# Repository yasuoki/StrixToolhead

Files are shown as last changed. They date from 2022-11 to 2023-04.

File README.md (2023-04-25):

# Strix Tool Head for VORON TRIDENT
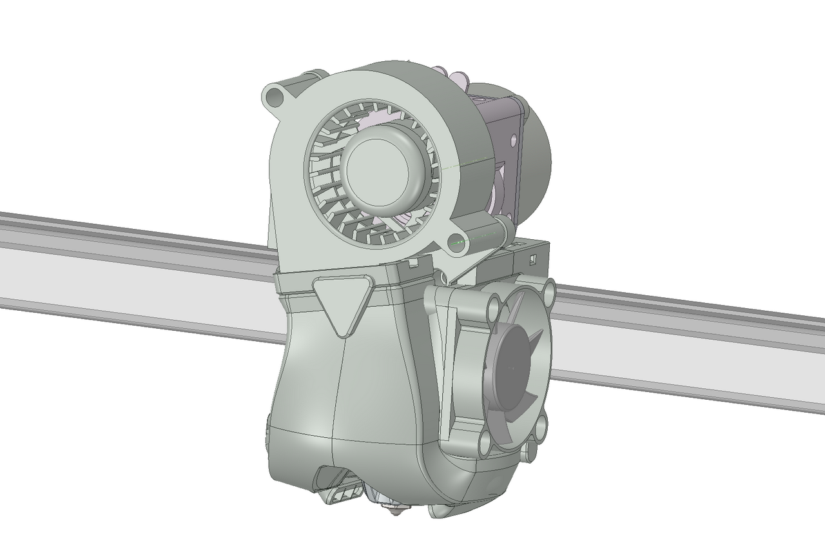
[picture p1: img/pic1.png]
<br>
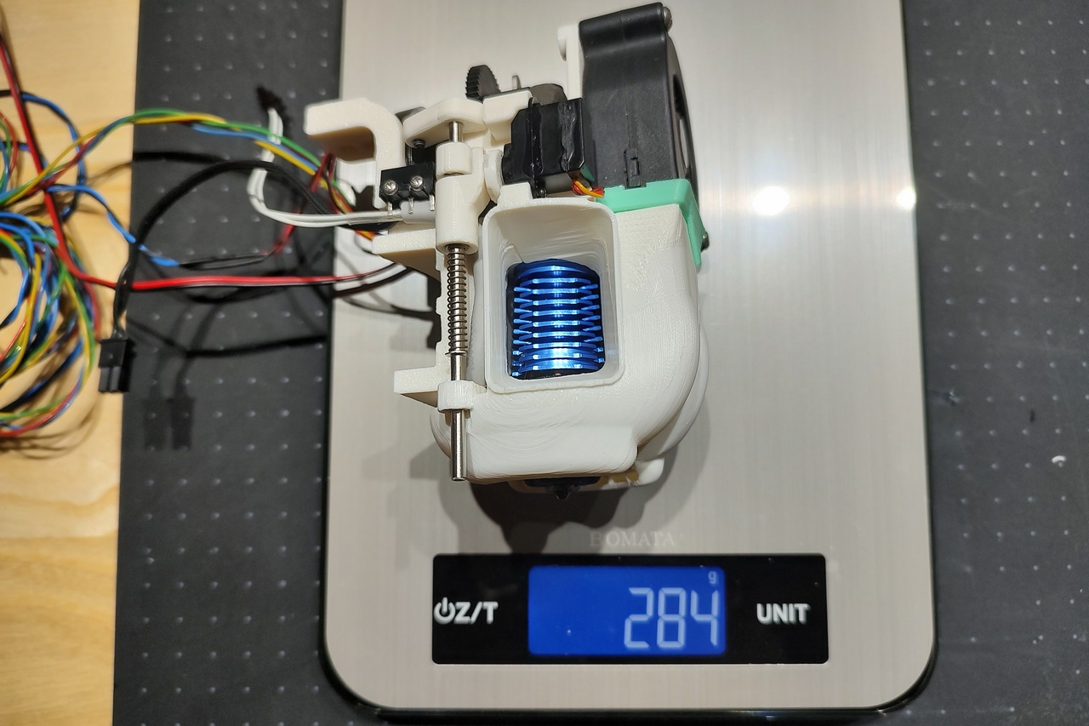
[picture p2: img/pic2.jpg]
<br>
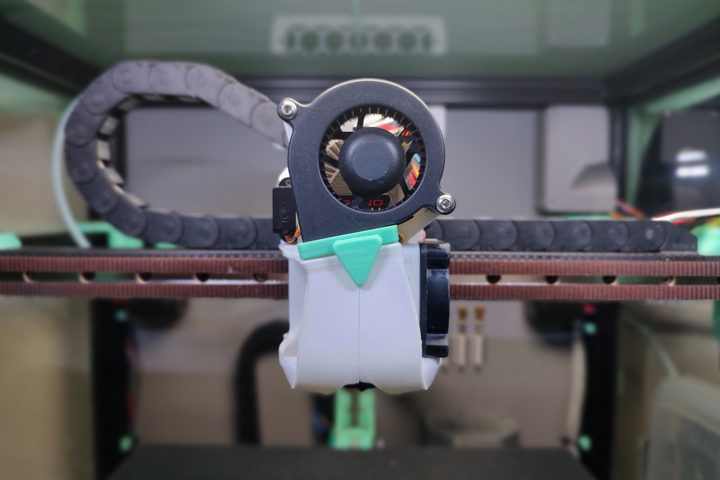
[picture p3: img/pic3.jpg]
<br>
(https://www.youtube.com/watch?v=hcAJJV4R7ww)<br>
(https://www.youtube.com/watch?v=_O_6WqJrIEA)

## Caution
This toolhead is still under development and has not yet been tested for stability.   
I am trying to design a better toolhead, but something could go wrong and your 3D printer could break.

## Features
- Short distance from the linear rail to the nozzle.
- Light weight. (290g or less)
- Optimized airflow.
- 5020 parts cooling fan.
- Built-in retractable Z-probe.
- Silent

## Probe Accuracy
~~~
PROBE_ACCURACY
PROBE_ACCURACY at X:150.000 Y:150.000 Z:5.133 (samples=10 retract=3.000 speed=10.0 lift_speed=10.0)
probe at 150.000,150.000 is z=2.132250
probe at 150.000,150.000 is z=2.133500
probe at 150.000,150.000 is z=2.134437
probe at 150.000,150.000 is z=2.134437
probe at 150.000,150.000 is z=2.134750
probe at 150.000,150.000 is z=2.134750
probe at 150.000,150.000 is z=2.133812
probe at 150.000,150.000 is z=2.134437
probe at 150.000,150.000 is z=2.133812
probe at 150.000,150.000 is z=2.134750
probe accuracy results: maximum 2.134750, minimum 2.132250, range 0.002500, average 2.134094, median 2.134437, standard deviation 0.000745
~~~

## Parts Printing
- Layer height 0.2mm, Extrusion width 0.4mm, Wall count 4, Top/Bottom layers 8, Infill 40%.
- Lightness and strength are prioritized over ease of printing, so most parts require support.
- Select ServoHorn2.2gA(B).stl and ServoHorn2gA(B).stl according to your servo motor
- Servo horns A and B differ in thickness by 0.2 mm. Select the one that fits.

## BOM
- M2.5 x 6mm BHCS x4 (for Rapido hotend)
- M3 x 8mm BHCS x4 (for linear rail)
- M3 x 10mm BHCS x7
- M3 x 25mm BHCS x2
- M3 x 35mm SHCS x2
- M2 x 10mm Self-Tapping Screw x2
- M1.7 x 3mm Flat Head Screw x1 (for servo horn)
- M1.7 x 5mm x2 (for servo mount)
- M3 x 6mm Set Screw x1
- M3 x 4mm Insert Nut x12
- 3mm(ID) x 5mm(OD) x 5mm(L) Sleeve Bearing(Oilless Bushings) x4
- 3mm(D) x 82mm(L) Stainless Steel Shaft x1
- 0.8mm(D) x 6mm(L) Piano wire x1 
- 2mm(ID) E-Clip x2
- 4mm(OD) x 0.4mm(RD) x 25mm(L) Compression Spring x1
- 26mm(L) PTFE Tube x1
- 7mm x 20mm x 0.5mm Carbon fiber plate x1 (Option)
- Micro Switch (OMRON D2F-01F Low operating force 0.74 N) x1
- Servo Motor 2.2g(Rrlandoo AS0022) or 2g(Dspower DS-M005) x1
- 5020 Blower Fan (Sunon GB1205PKV3-8AY or GDSTIME GDB5030) x1
- 4010 Axial Fan x1
- Phaetus Rapido HF x1
- Bondtech LGX Lite x1

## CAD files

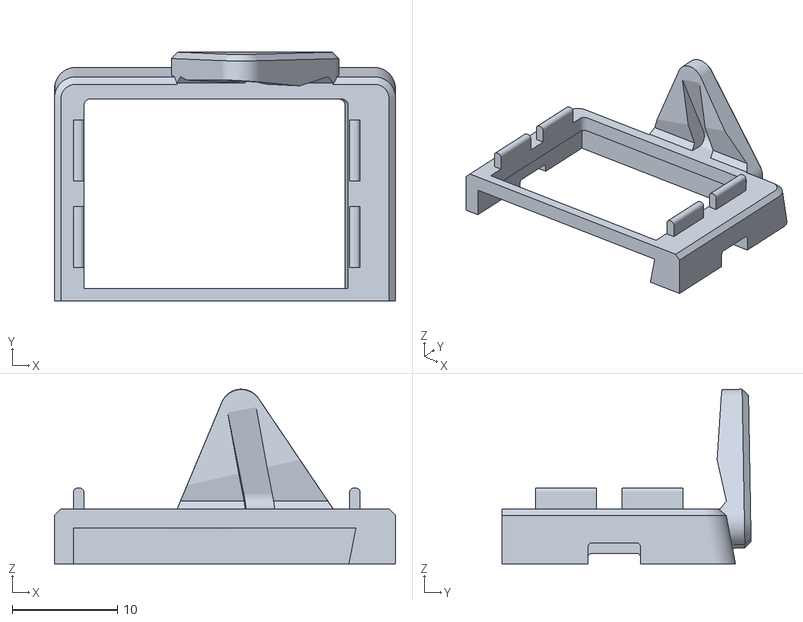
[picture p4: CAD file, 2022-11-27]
STLs/BlowerFlange.stl
32.4 x 23.7 x 16.6

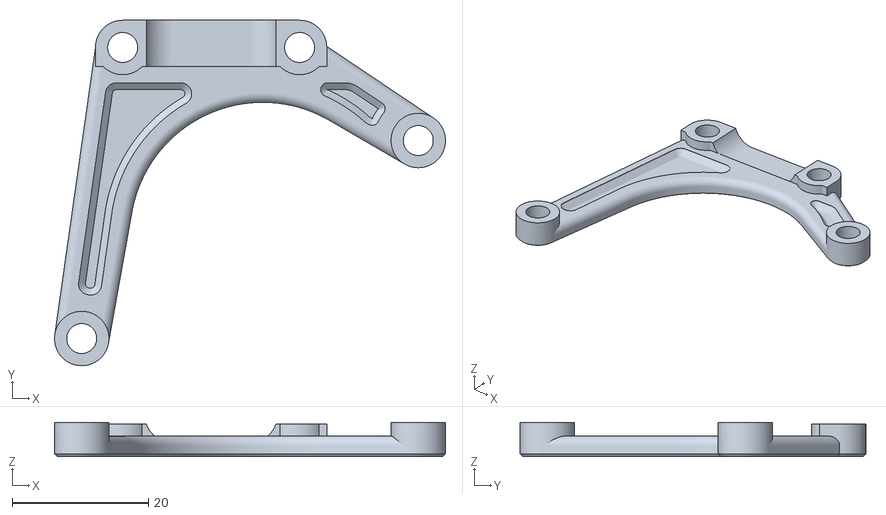
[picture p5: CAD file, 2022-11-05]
STLs/BlowerMount.stl
57.5 x 50.8 x 5.00

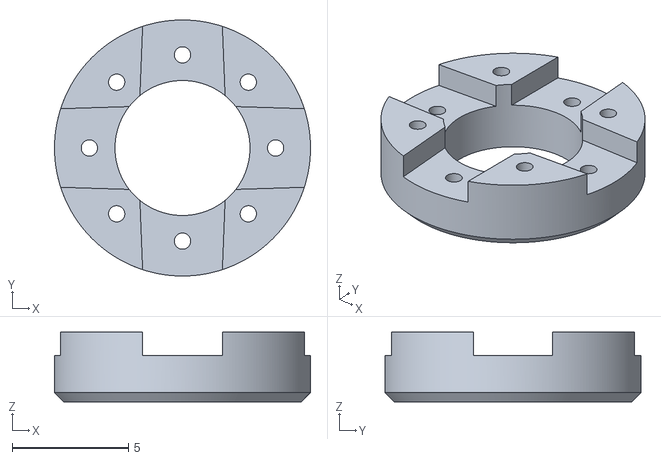
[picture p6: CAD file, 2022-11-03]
STLs/ServoHorn2gA.stl
11.0 x 11.0 x 3.00

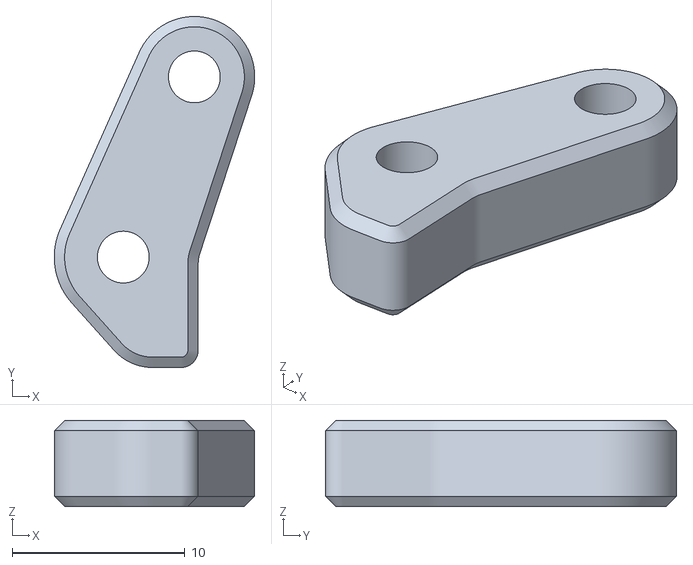
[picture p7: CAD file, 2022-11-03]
STLs/SensorTrigger.stl
11.6 x 20.3 x 5.00

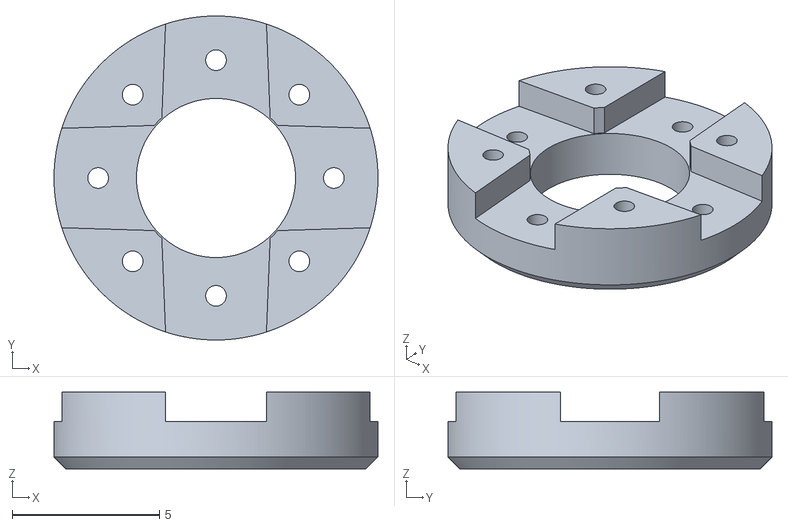
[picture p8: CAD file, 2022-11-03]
STLs/ServoHorn2.2gB.stl
11.0 x 11.0 x 2.60

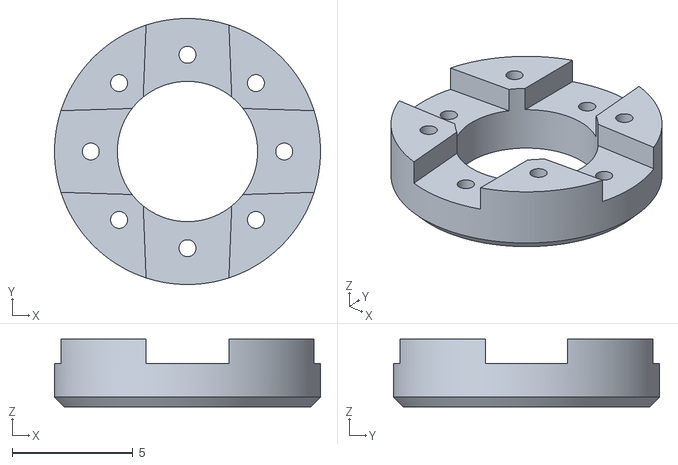
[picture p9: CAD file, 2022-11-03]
STLs/ServoHorn2gB.stl
11.0 x 11.0 x 2.80

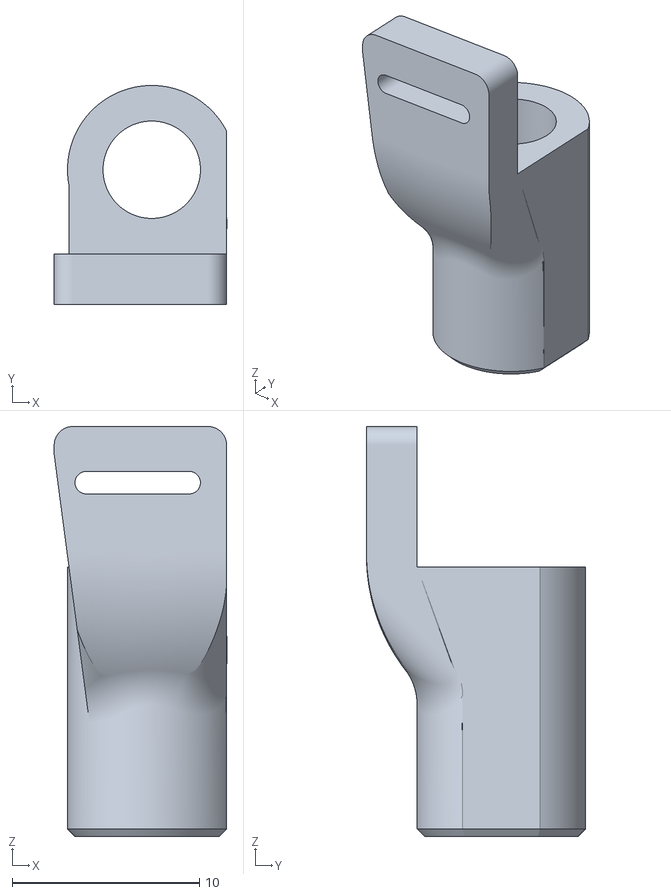
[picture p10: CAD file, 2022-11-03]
STLs/SensorElevator.stl
9.22 x 11.7 x 21.9

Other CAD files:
STLs/ServoHorn2.2gA.stl

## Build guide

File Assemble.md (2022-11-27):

## Insert nuts
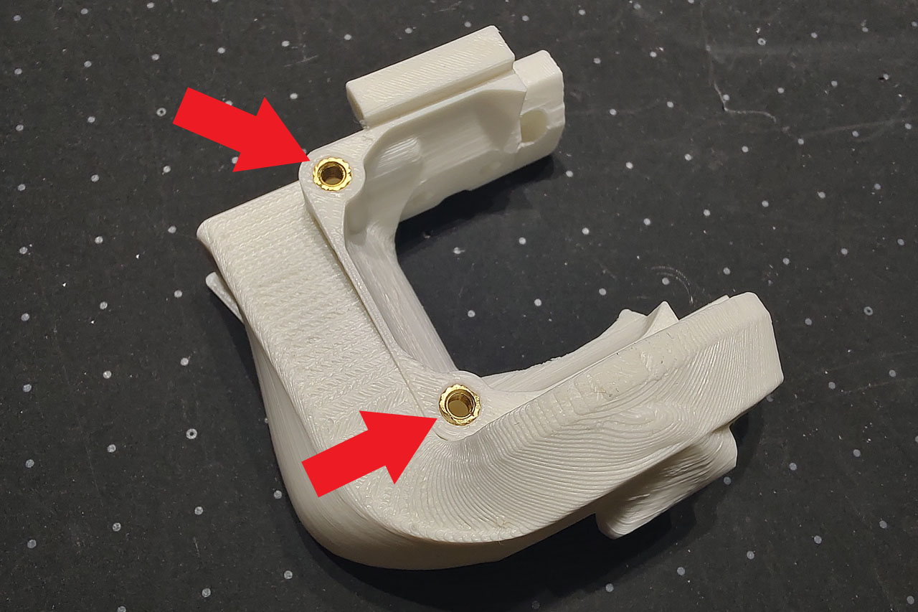
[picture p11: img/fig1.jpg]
<br>
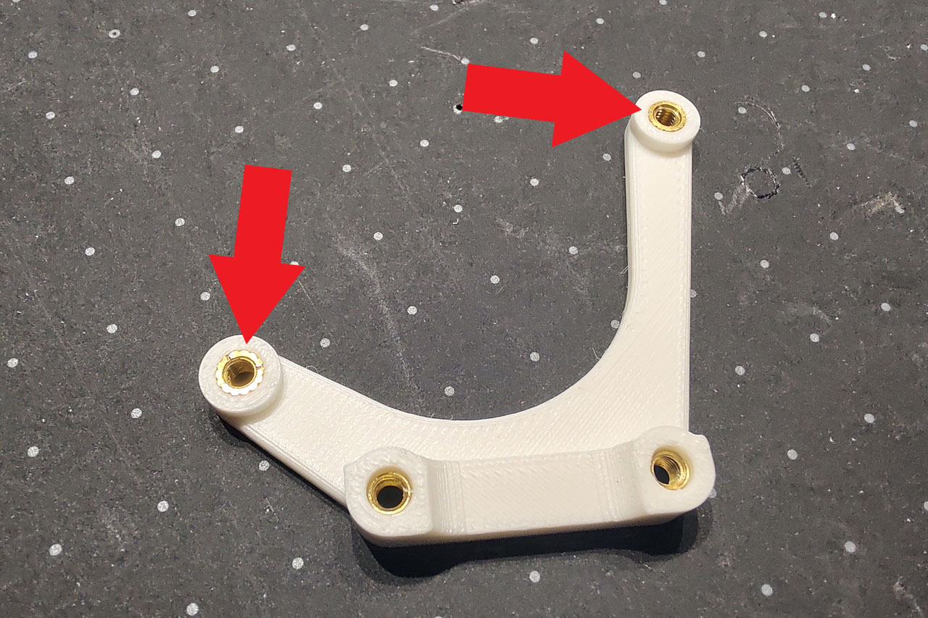
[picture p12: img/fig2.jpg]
<br>
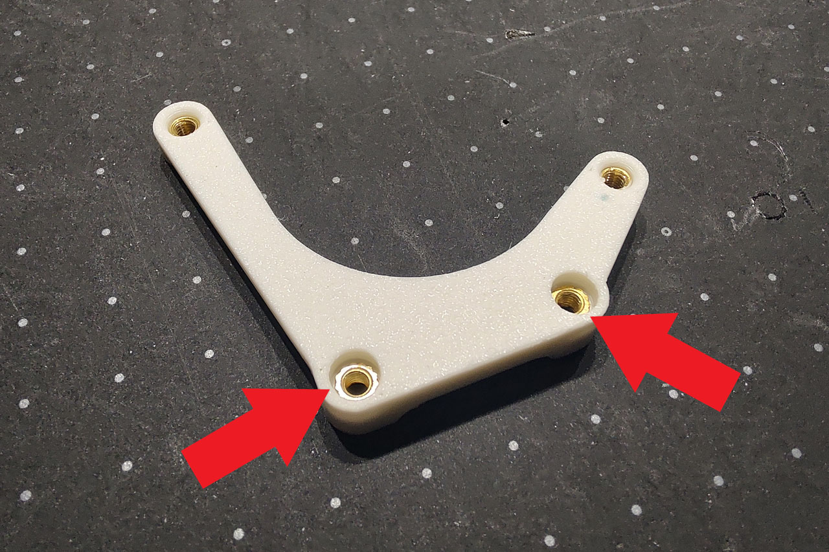
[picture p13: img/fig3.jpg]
<br>
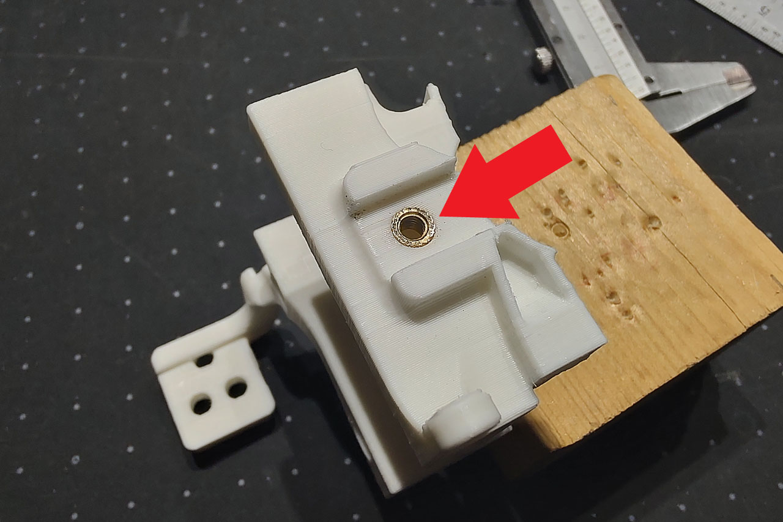
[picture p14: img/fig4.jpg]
<br>
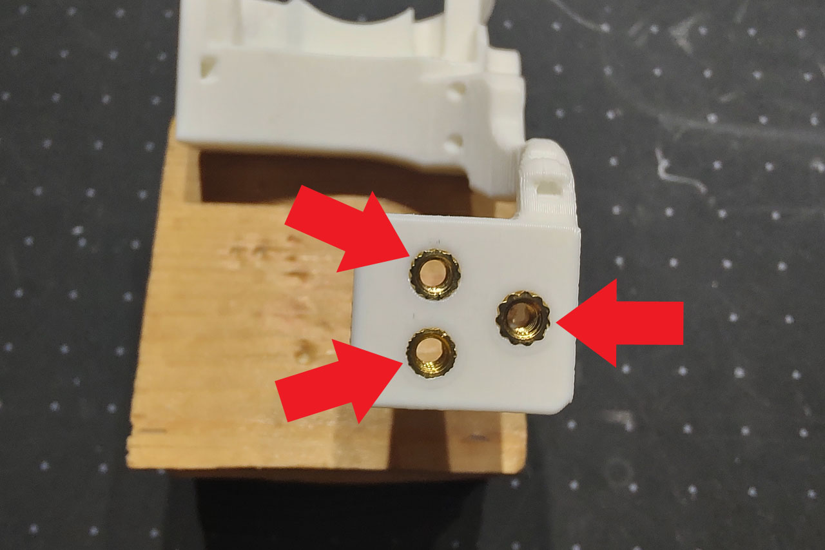
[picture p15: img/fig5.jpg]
<br>
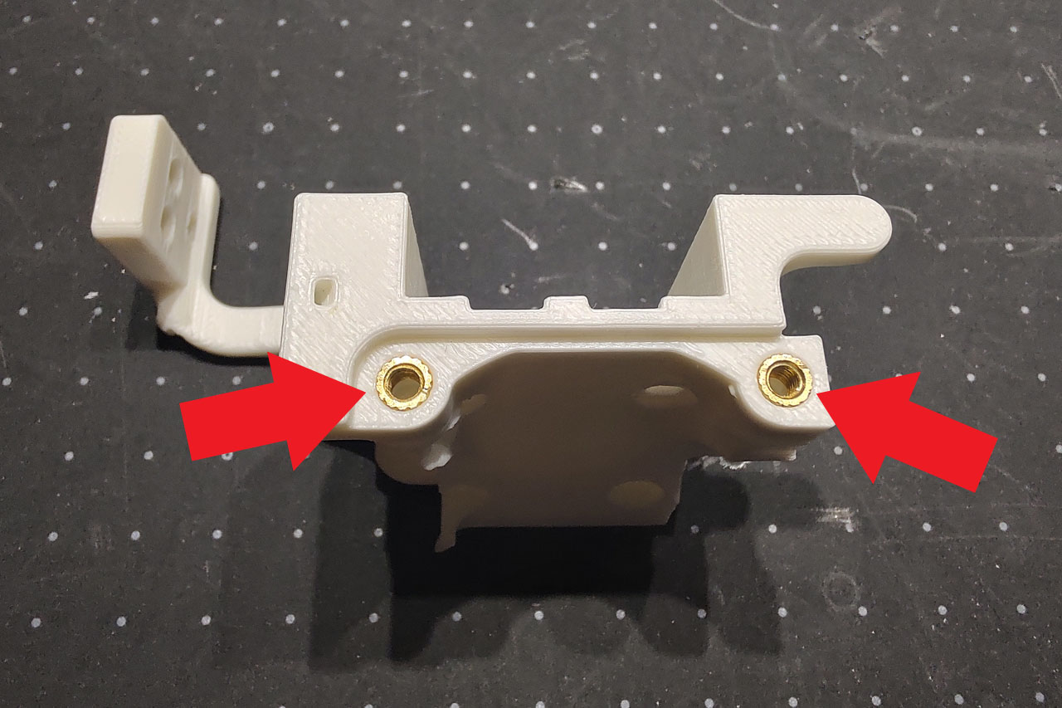
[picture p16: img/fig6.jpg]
<br>

## Sleeve bearings
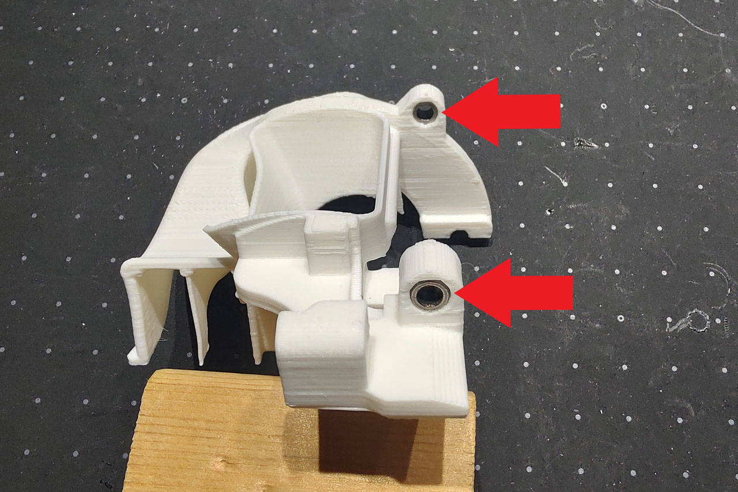
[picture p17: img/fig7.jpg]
<br>
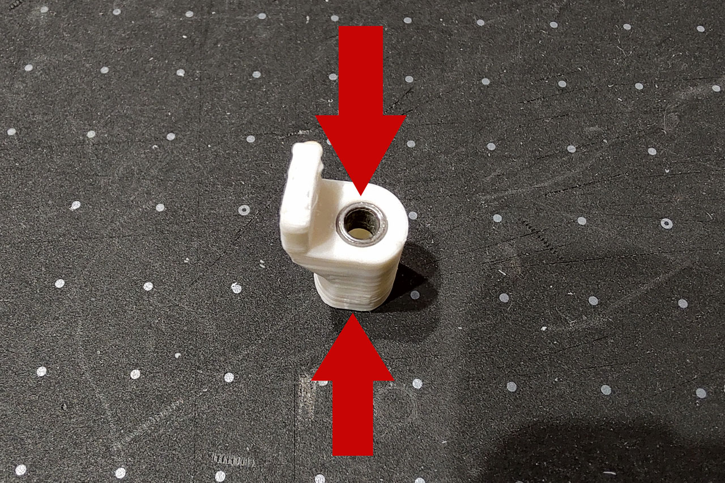
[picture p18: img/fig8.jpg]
<br>

## Z Probe
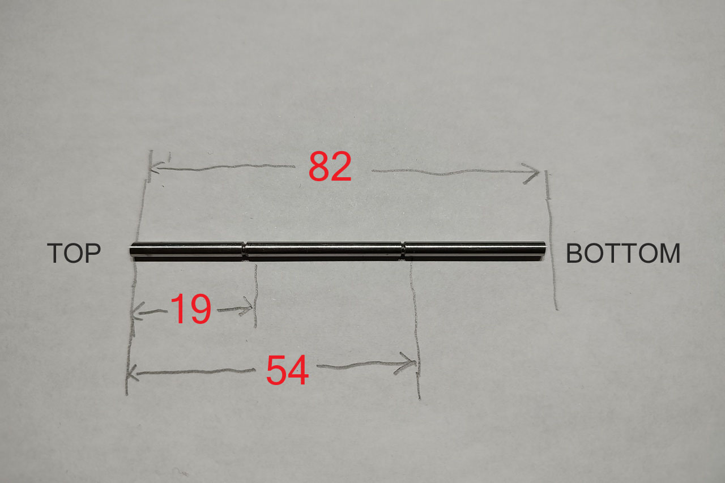
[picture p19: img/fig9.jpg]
<br>
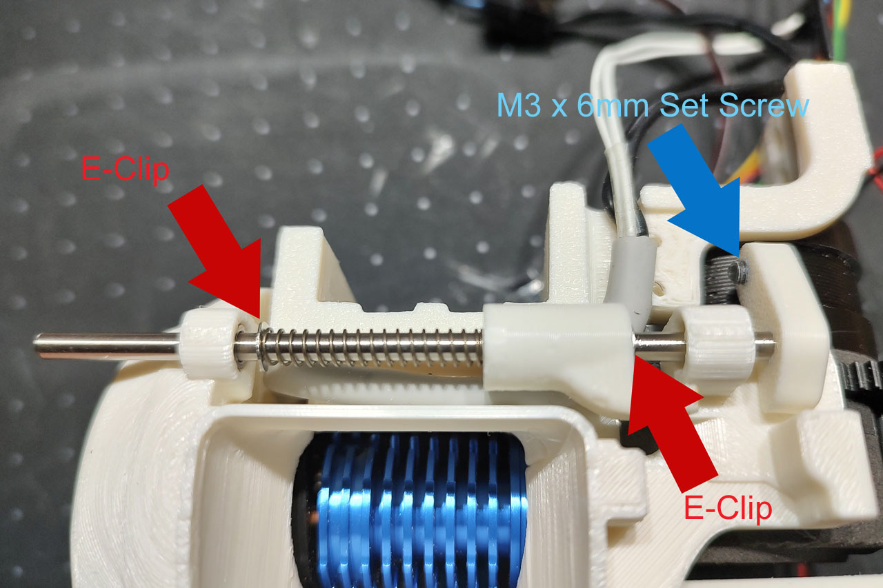
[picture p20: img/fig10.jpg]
<br>
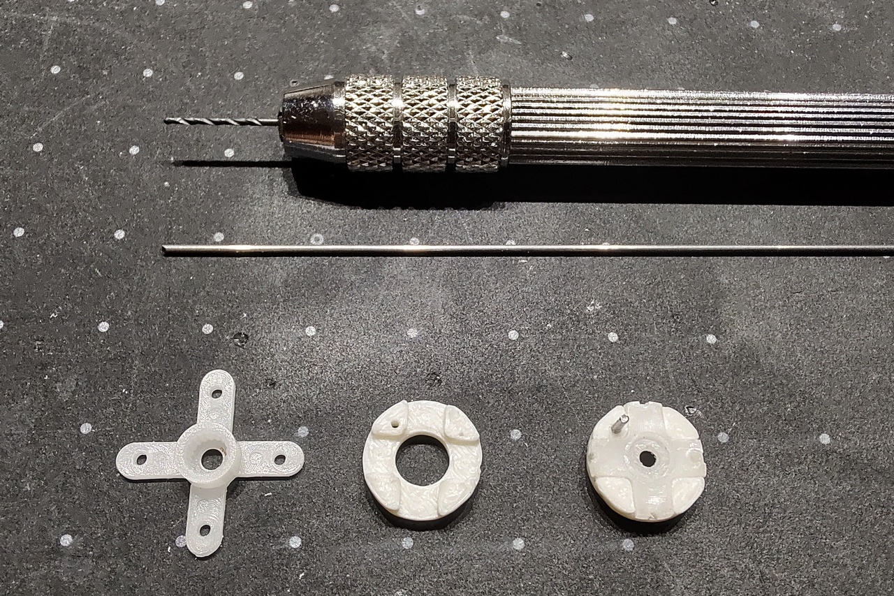
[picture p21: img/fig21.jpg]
<br>
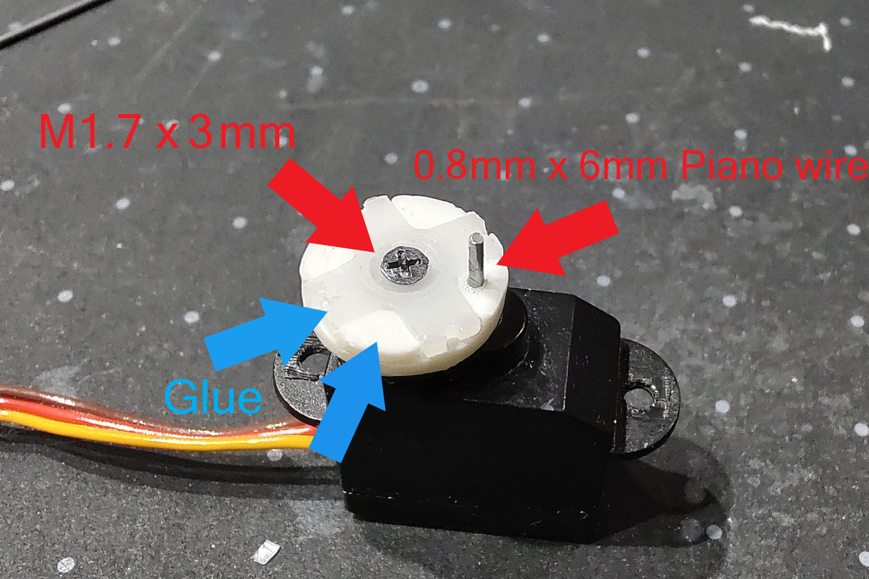
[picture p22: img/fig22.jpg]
<br>
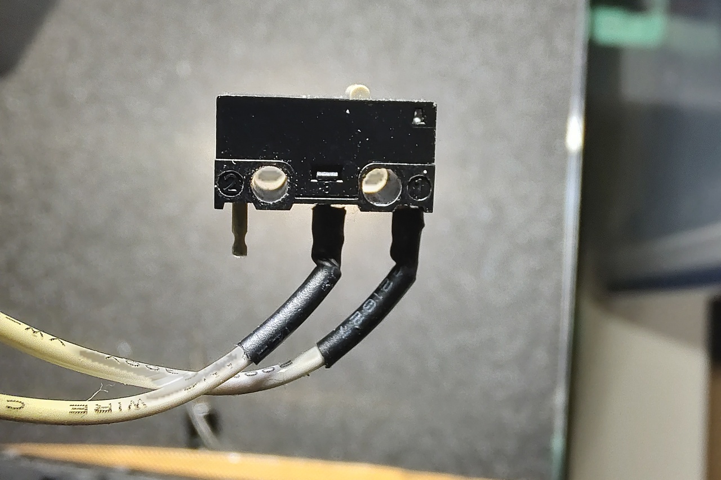
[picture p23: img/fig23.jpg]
<br>

## Hotend
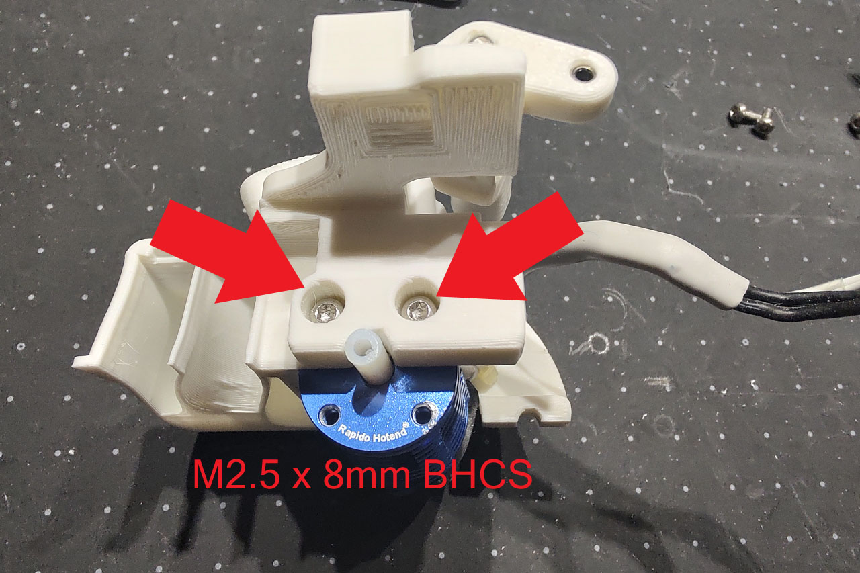
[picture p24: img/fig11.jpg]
<br>
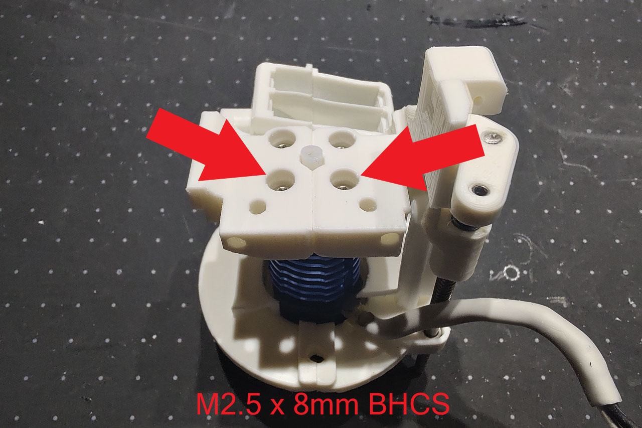
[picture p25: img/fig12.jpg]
<br>

## Extruder
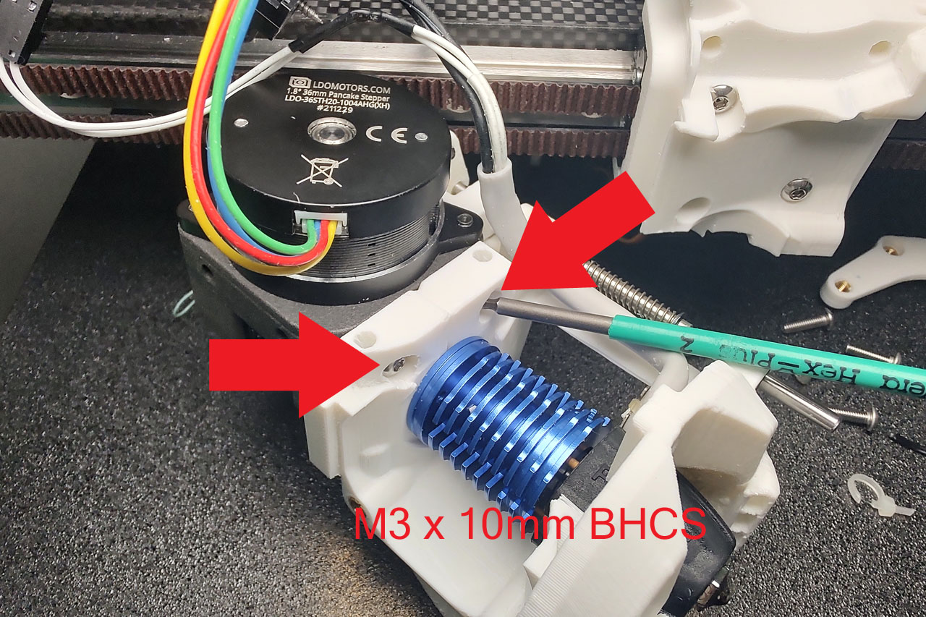
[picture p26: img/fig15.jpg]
<br>

## Mounting on Rail
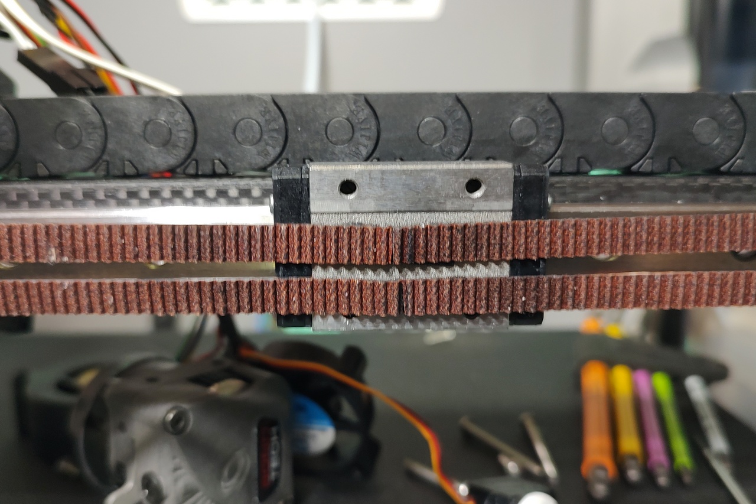
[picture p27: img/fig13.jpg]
<br>
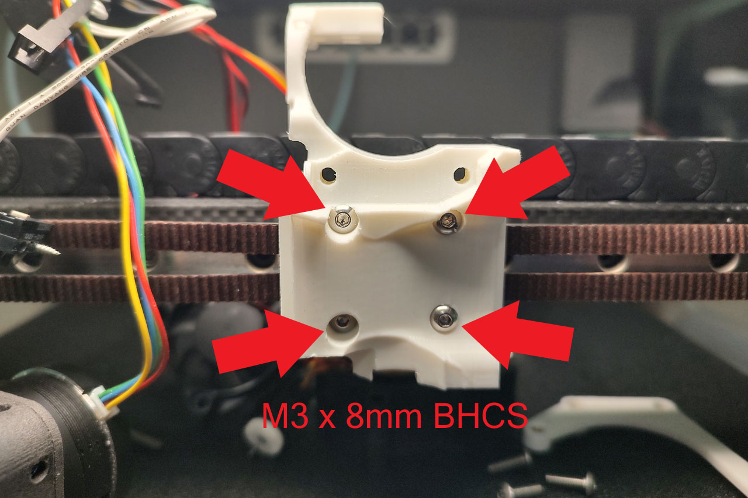
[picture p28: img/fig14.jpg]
<br>
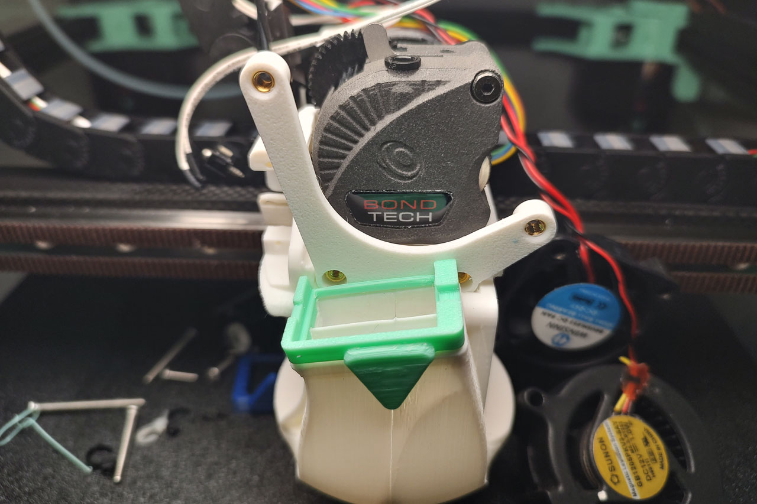
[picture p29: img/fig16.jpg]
<br>
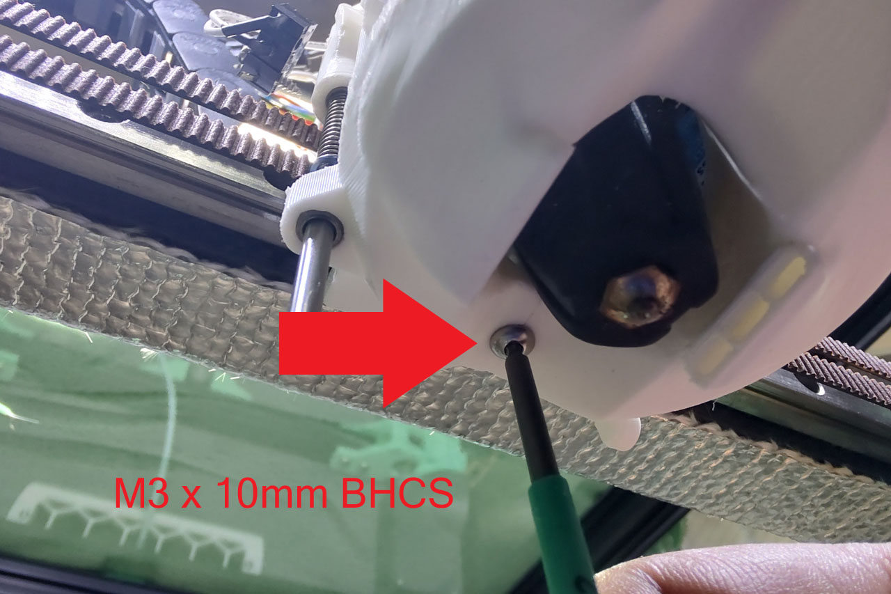
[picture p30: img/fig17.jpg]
<br>
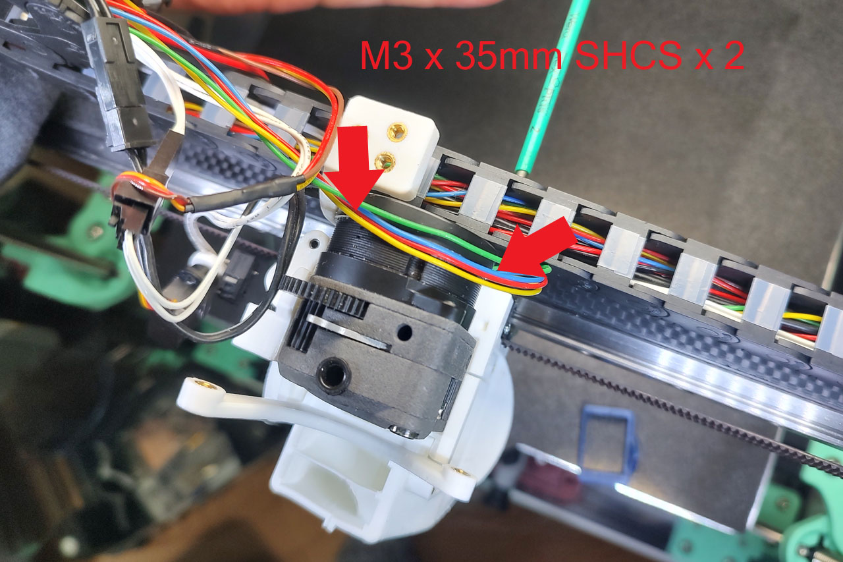
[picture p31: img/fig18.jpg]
<br>

## Parts cooling fan
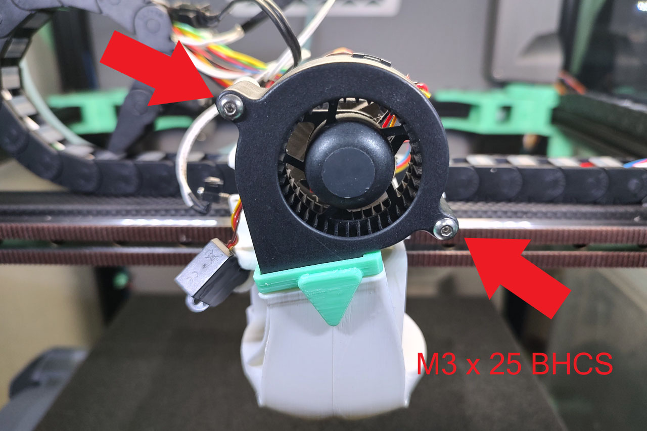
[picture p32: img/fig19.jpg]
<br>

## Hotend cooling fan
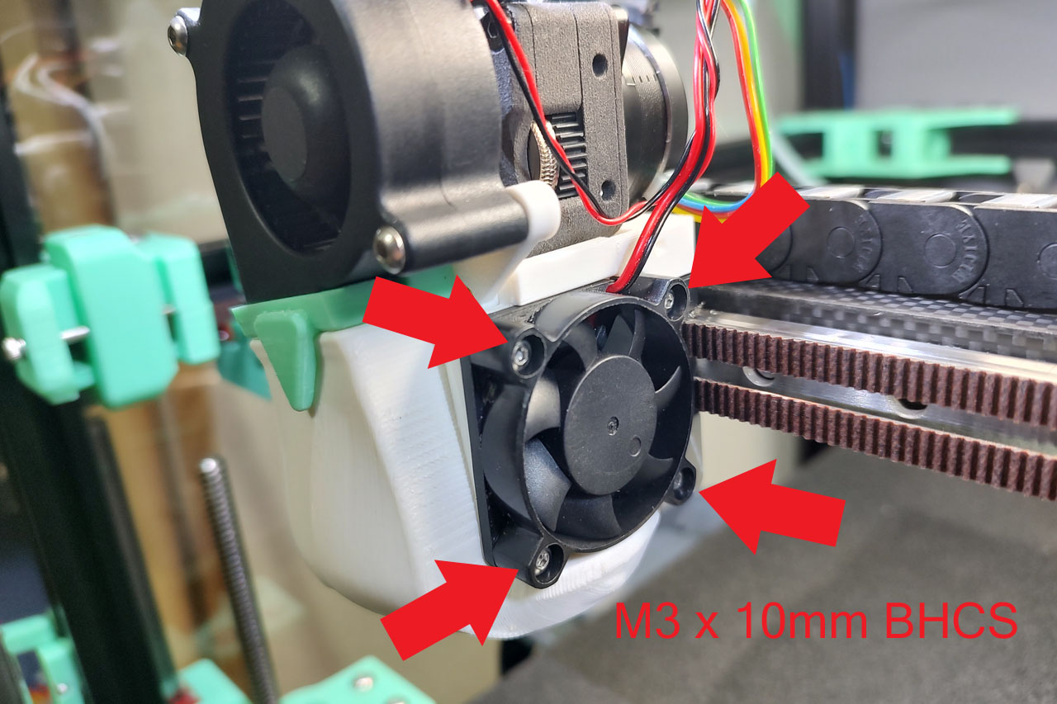
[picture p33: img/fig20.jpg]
<br>

## Microswitch and Servo
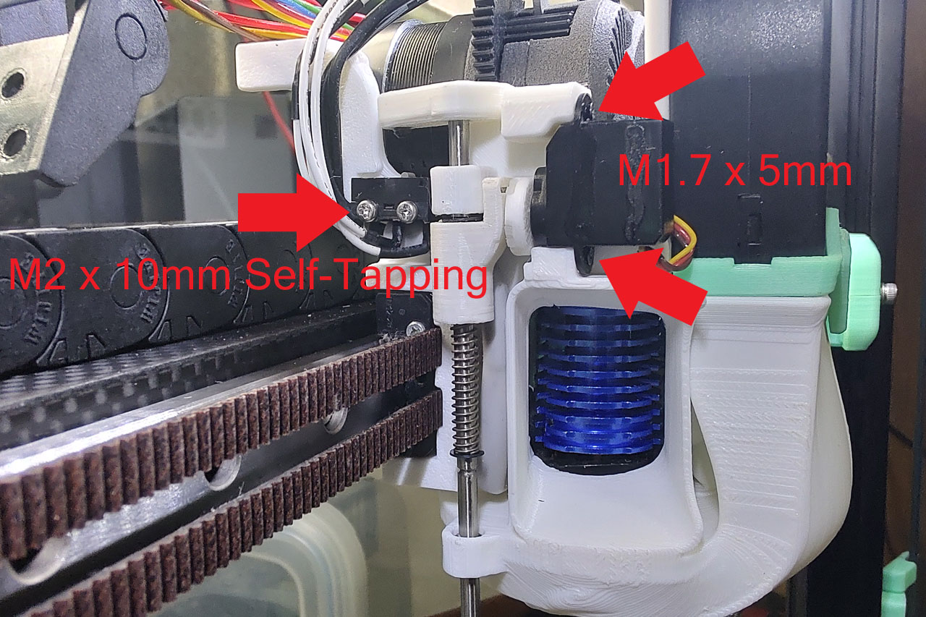
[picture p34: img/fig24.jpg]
<br>

## X End Stop
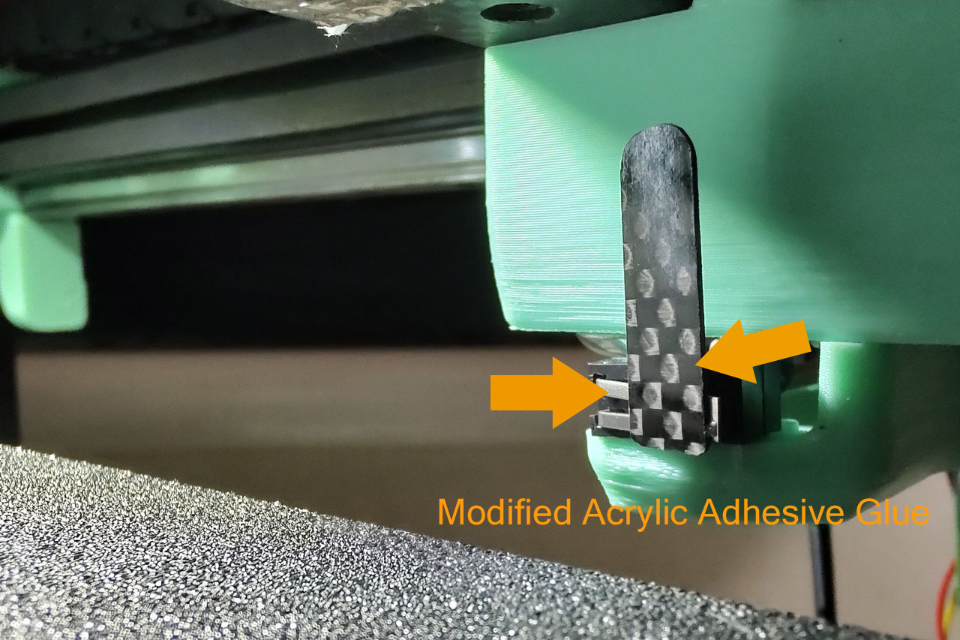
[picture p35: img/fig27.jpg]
<br>
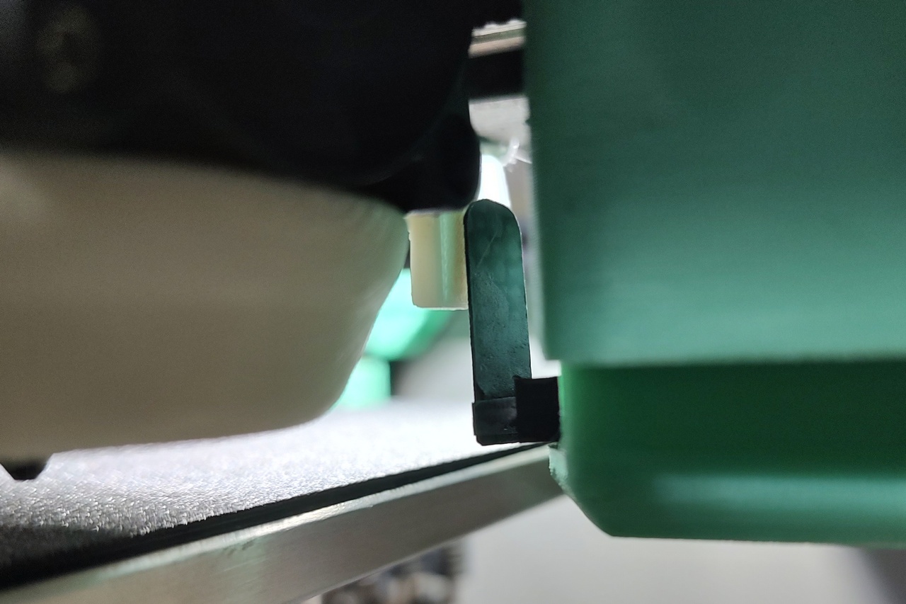
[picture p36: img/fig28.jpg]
<br>

## Wirering
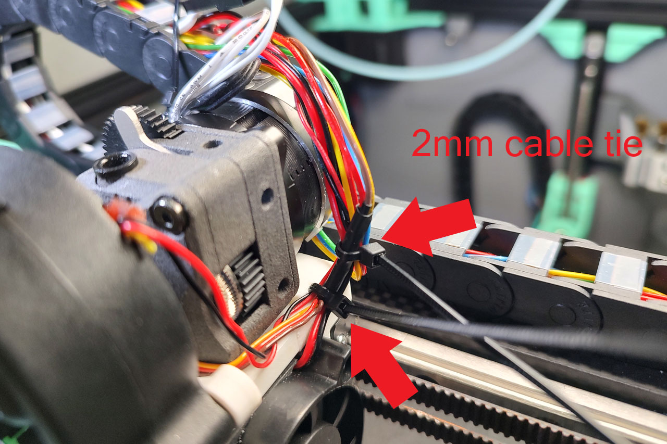
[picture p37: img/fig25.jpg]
<br>
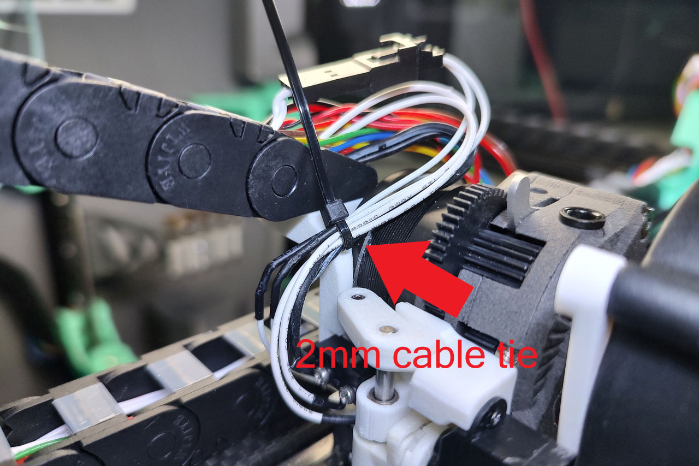
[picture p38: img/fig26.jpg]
<br>
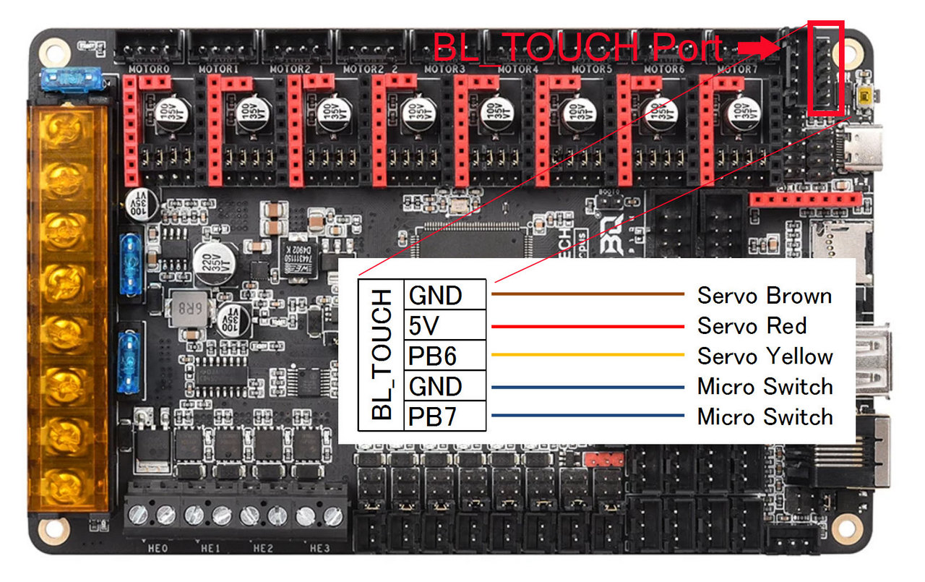
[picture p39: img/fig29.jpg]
<br>

## Configuration
~~~
#####################################################################
#   Retractable Probe Servo
#####################################################################
[servo RetractableProbe]
pin: PB6
initial_angle: 0
maximum_servo_angle = 180
minimum_pulse_width = 0.0005
maximum_pulse_width = 0.0024

[gcode_macro PROBE_OUT]
gcode:
    SET_SERVO SERVO=RetractableProbe ANGLE=180
    G4 P800

[gcode_macro PROBE_IN]
gcode:
    SET_SERVO SERVO=RetractableProbe ANGLE=0
    SET_SERVO SERVO=RetractableProbe WIDTH=0
    G4 P800

#####################################################################
#   Probe
#####################################################################
[probe]
pin: ^PB7
x_offset: -27.49
y_offset: 13.85
z_offset: 0
speed: 10.0
samples: 3
samples_result: median
sample_retract_dist: 3.0
samples_tolerance: 0.006
samples_tolerance_retries: 3
deactivate_on_each_sample: False
activate_gcode:
    PROBE_OUT
deactivate_gcode:
    PROBE_IN
~~~

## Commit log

2022-11-05 Modified airflow for part cooling
    [BlowerFlange.stl, BlowerMount.stl]
2022-11-05 Tie-wrap anchors for wiring added
2022-11-27 Updated parts cooling airflow Additional body anchorage points to improve strength Replaced document images
    [BlowerFlange.stl]
2022-11-27 BodyRight.stl bug fix
2022-11-27 Adjust STL file resolution
